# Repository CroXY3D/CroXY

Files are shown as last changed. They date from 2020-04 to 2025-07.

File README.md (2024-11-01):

# CroXY
CroXY is a Crossed Gantry 3D Printer.  Pronounced "Crock-see".  

Designed and built by Wes Cherry (Ocho Camino, wesc@technosis.com) with help from CLedbetter.

CroXY is a fully enclosed 3D CrossXY printer with a crossed linear rail gantry design, direct drive extruder and a kinematically mounted bed that moves in Z with reduced triple belt drive. 

Version 3 is nearing Beta.   

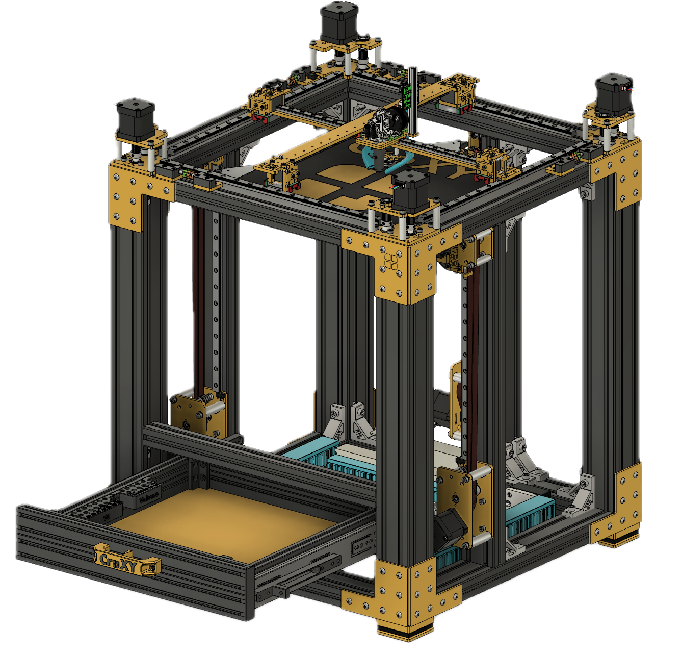
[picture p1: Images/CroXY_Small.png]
Small Image of CroXY
 
  
It is simple to build, align and provision.  The design requires no printed parts aside from the cooling duct.   Print quality is superb. 

The printer has been assembled and is printing with excellent print quality for a many years now.  It is in active development. 

# Major features of CroXY
  - All metal design (Except for cooling duct).  CroXY uses the Ice Cream Sandwich design pattern where printer structures are made from laser cut aluminum plate with standoffs.
  - 3060 frame members for stiffness and ease of assembly.  Corner towers can be 6060.
  - Crossed rail gantry design with 4 motors (5mm or 8mm shafts) driving 9mm or 12mm XY belts.  Motor shafts are supported with a bearing on their end to reduce flex.
  - Triple 4:1 9mm belt driven Z for automatic bed levelling.
  - Linear Rails except the cross rails are MGN12H. 
  - Cross rails are MGN9H for less moving mass.  Both cross rails are backed by a flat 4.7mm thick 6061 aluminum backer.  Extensive FEA simulations have been performed on the gantry.
  - Fully Enclosed, Coming soon!   
  - Bed is 6 to 12mm cast aluminum and is kinematically mounted with Maxwell kinematic joints preloaded by magnets. 
  - Extruders supported: LGX Lite, VZ Hextrudort and Orbiter.
  - Hotends supported: Goliath water and air cooled, Chube.
  - Part cooling is CPAP or dual Axial 4028 fans
  - Magnetically coupled switch based probe (Euclid) picked up from a dock for super accurate bed probing.  Repeatibility of nearly 0.001mm.
  - Simple, easily accessible belt tensioning.
  - Dedicated area for nozzle purge and wipe. 
  - Z Towers are built on a single 3060 extrusion.  They easily remove from the printer for bench work.
  - BTT Octopus, Fysetc Spyder with Klipper, Duet2 or Duet3 electronics with Reprap firmware 3.
  - Electronics are in the bottom of the machine, for easy access from above.  No flipping or rotating the machine to access the electronics.
  - Nearly all wires are run thru the center channel of 3060/6060 extrusions for a clean looking machine.
  - Built in optional drawer for tools and or a spool that feeds the extruder.  
  - Hour meter.
  - LED status rings, similar to BLV MGN Cube.
  - Feet with sorbothane vibration isolation.
  - Footprint comparable to other printers of same bed size (Footprint is only 5% larger than that of a comparable print volume Railcore)
  - CAD is for 300x300x300 nominal size.  CroXYs as small as 200^3 and as large as 500x350x350 have been built. 

# CroXY offers a number of advantages over CoreXY designs
  - Belts are shorter and have simple paths, alignment is easier and less ringing
  - Belts can be as wide as 12mm for more accurate positioning and less ringing compared to 6mm wide belts.
  - Less friction in motion system makes for more accurate positioning making for exceptional layer stacking.
  - 4 motors moving the XY gantry make for more torque for more accurate positioning (1.4x-4x more torque)
  - Motion is simple X motors move X, Y motors move Y, so troubleshooting is easier
  
# Disadvantages of CroXY
  - Requires 3 more rails and 2 more steppers/drivers than a CoreXY.
  - Visibility of the build area is lessened.  Though the printhead has been designed with nozzle visibility in mind.
  - Toolchanging is more difficult, but it is possible.
  - Cost.  It's not a cheap build.
  
# Work to be done 
  - Finish lid and enclosure, including front hinges
  - Wiring diagram
  - Chamber heater
  
# CAVEATS
CroXY is an advanced build.  You should only attempt to build it if you have successfully built another kit printer.  Building that will give you a lot of experience so you don't make mistakes with CroXY.  

Croxy is a ever growing experimental project. Although the existing machines work and work well, there is no guarantee that yours will. These are homemade machines built by different people, with differing parts. We help where we can, but in the end this is a hobby and we are hobbiests.

# DISCORD
We now have a [Discord](https://discord.gg/ryj6wyx) to discuss CroXY!  

# BOM  
A CroXY build will cost approx $XXXX with budget rails.  A first class build with Misumi rails will run around $XXXX. 

# SOURCE FILES
CroXY is fully open source with .STP files provided.  Please check the license (Creative Commons Attribution-NonCommercial-ShareAlike 4.0 International) before modifying or deriving from CroXY.  Commercial use or sale of CroXY derived designs is prohibited without approval.

# MEDIA

The images are quite old.  Will update soon.

[Video of CroXY](https://youtu.be/Kx4VfzS_V6c)

[Video of CroXY bed probiing and automatic bed levelling](https://www.youtube.com/watch?v=WyJbbjh8Hpk)

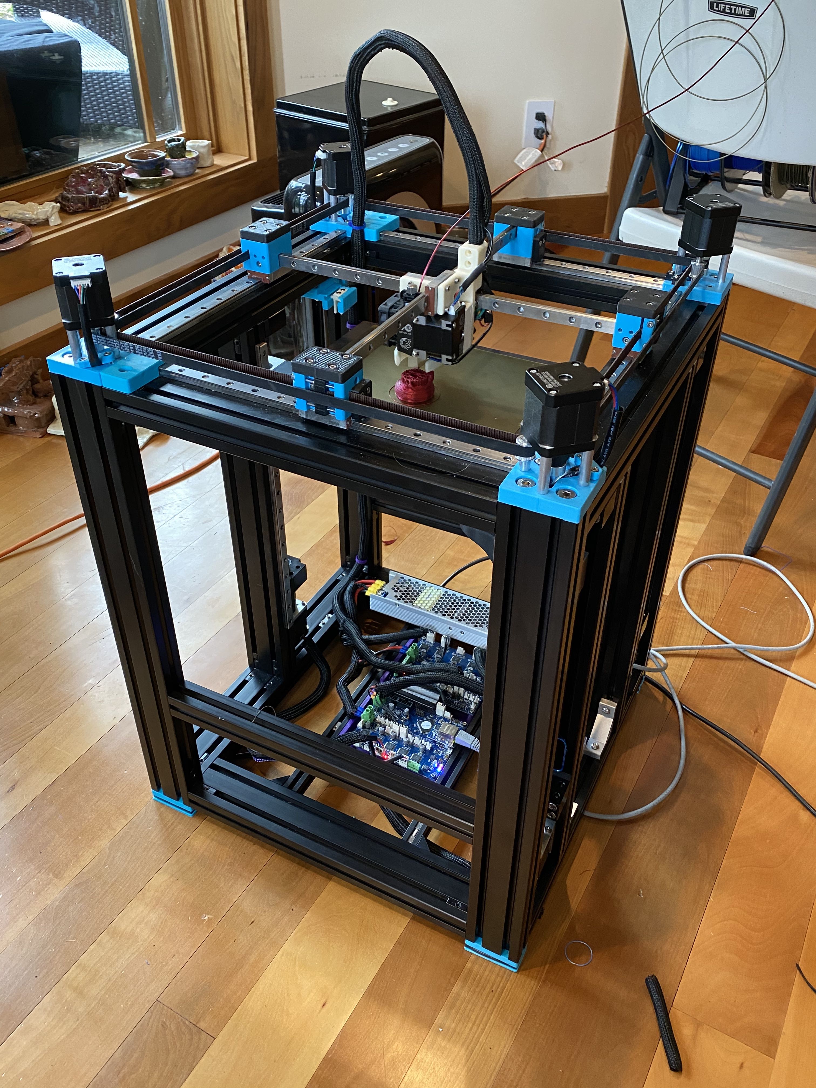
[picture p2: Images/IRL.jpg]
IRL


Older picture of CroXY.  It currently looks like the renderings IRL.

Image of CroXY
  
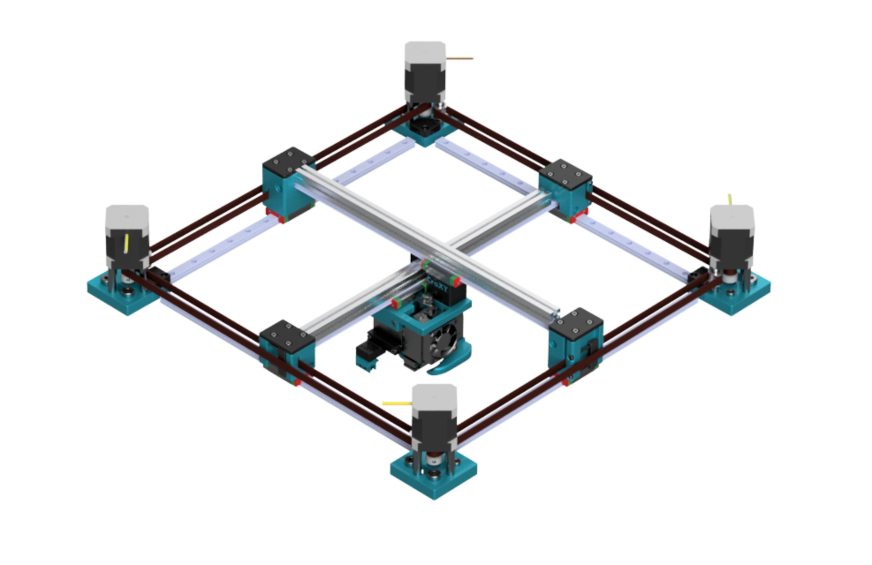
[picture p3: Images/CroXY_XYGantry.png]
Image of CroXY XY Gantry


XY Gantry

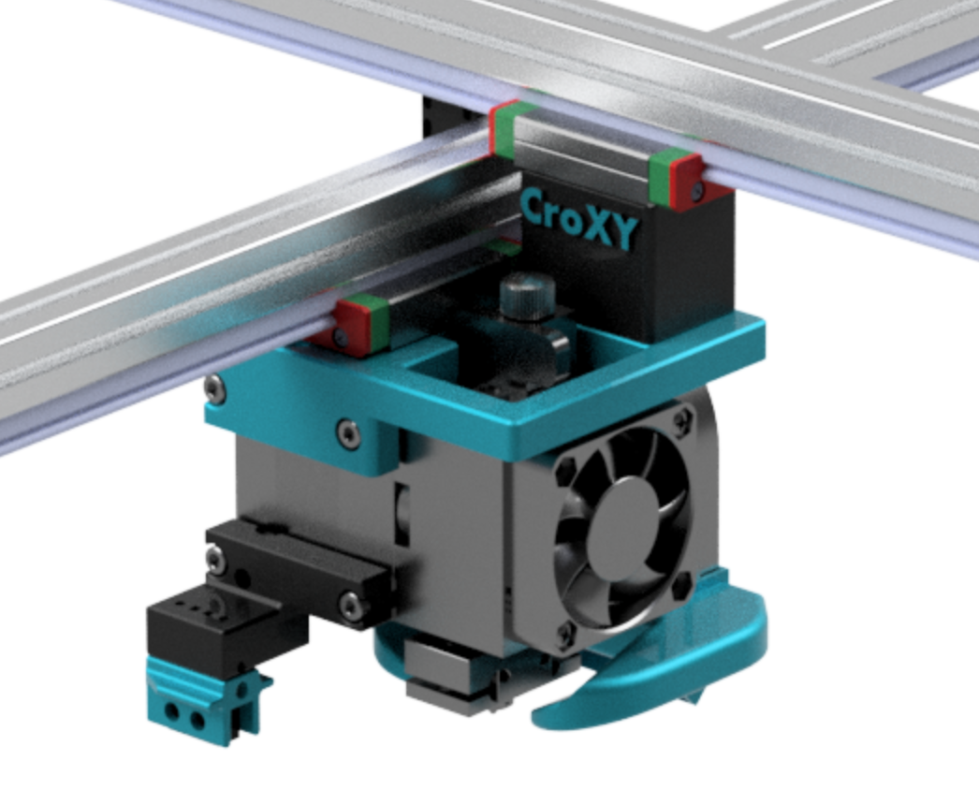
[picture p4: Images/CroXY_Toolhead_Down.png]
Image of CroXY Toolhead Down


Toolhead

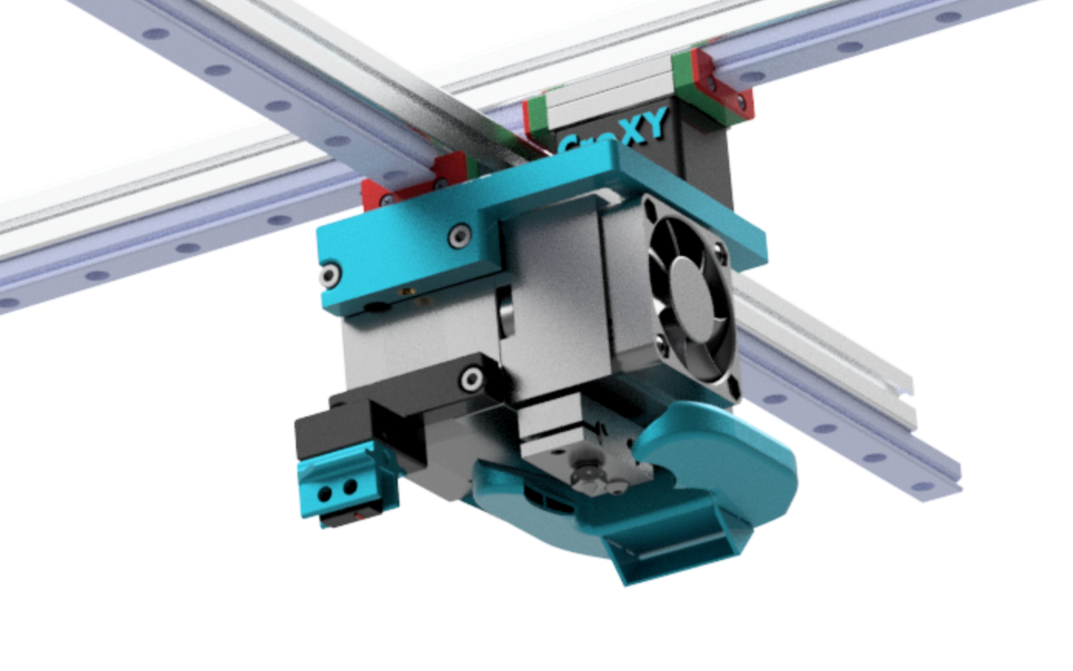
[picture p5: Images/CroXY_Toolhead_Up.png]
Image of CroXY Toolhead Up


Toolhead

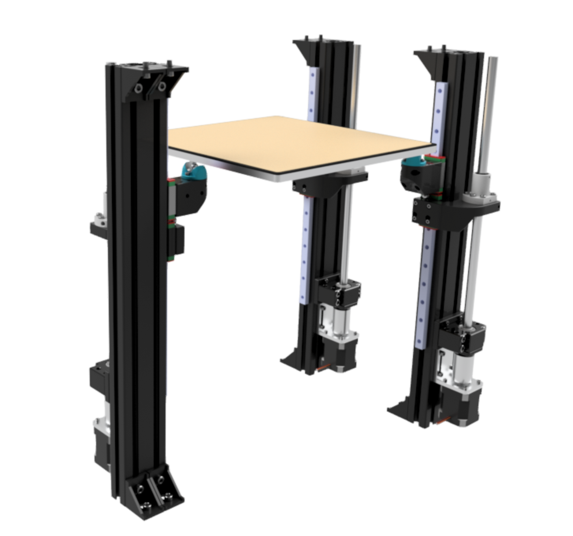
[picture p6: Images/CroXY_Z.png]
Image of CroXY Z


Z and Bed

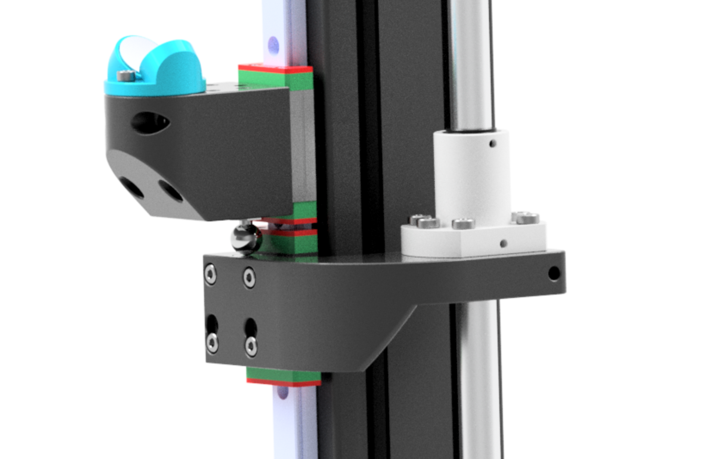
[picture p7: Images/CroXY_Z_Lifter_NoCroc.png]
Image of CroXY Z Lifter NoCroc


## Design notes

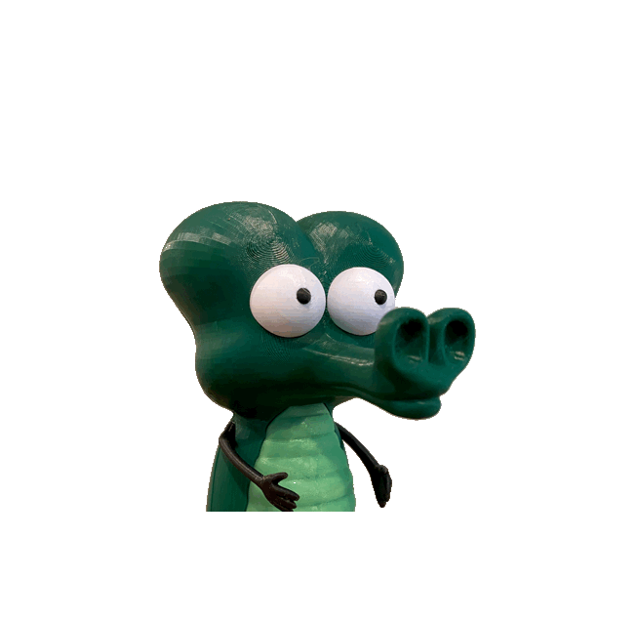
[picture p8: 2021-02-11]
Images/Discord/CroxyTransparentWideMargins.png

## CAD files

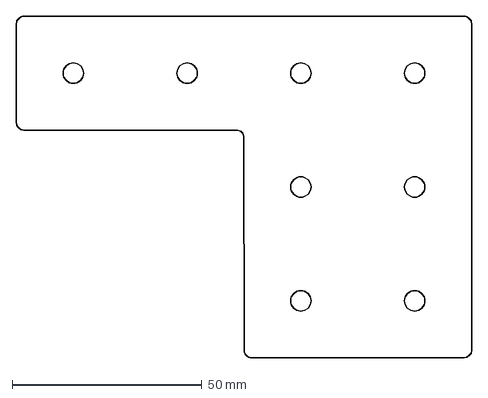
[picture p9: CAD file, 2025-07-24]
DXF/Frame/Corner_Bracket_3_3060CornerPost_x7_6060CornerPost_x15.DXF
120.0 x 90.0 mm

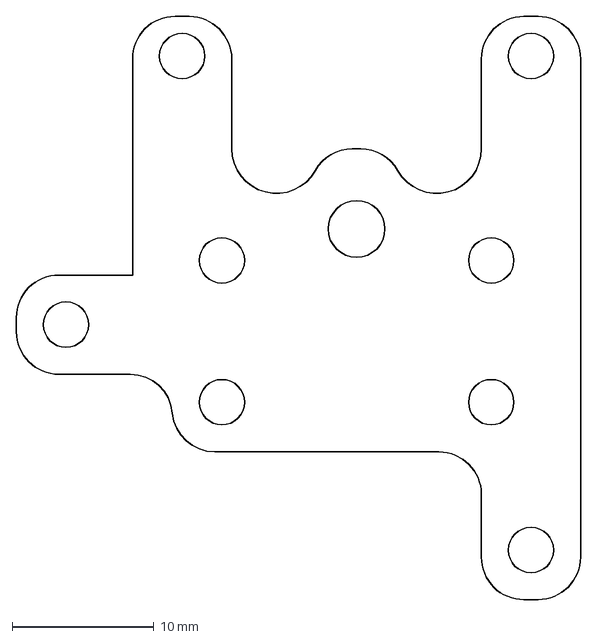
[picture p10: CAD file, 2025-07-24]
DXF/HeLGX_Adapter_3_X1.DXF
39.8 x 41.2 mm

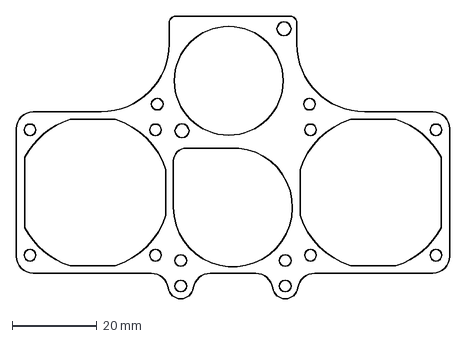
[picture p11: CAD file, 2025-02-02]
DXF/Tool/T_PCF_Axial_Fan_Adapter_3_x1.DXF
102.0 x 66.5 mm

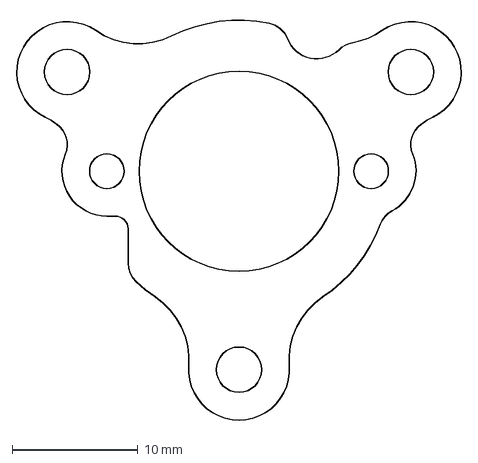
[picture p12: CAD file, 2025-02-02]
DXF/XY/XY_Motor_Bearing_Housing_5_x4.DXF
35.4 x 32.3 mm

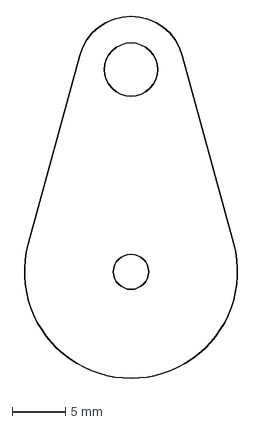
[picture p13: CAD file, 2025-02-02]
DXF/Z/Z_Maxwell_Spring_1_SpringSteel_x3.DXF
21.5 x 34.6 mm

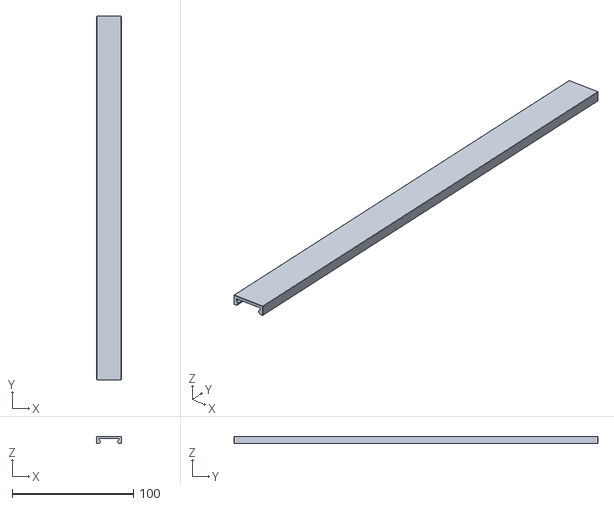
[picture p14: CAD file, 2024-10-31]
STL/Electronics/A-Cable_Duct_2020_300mm_Cap-T.stl
20.3 x 300.0 x 6.00

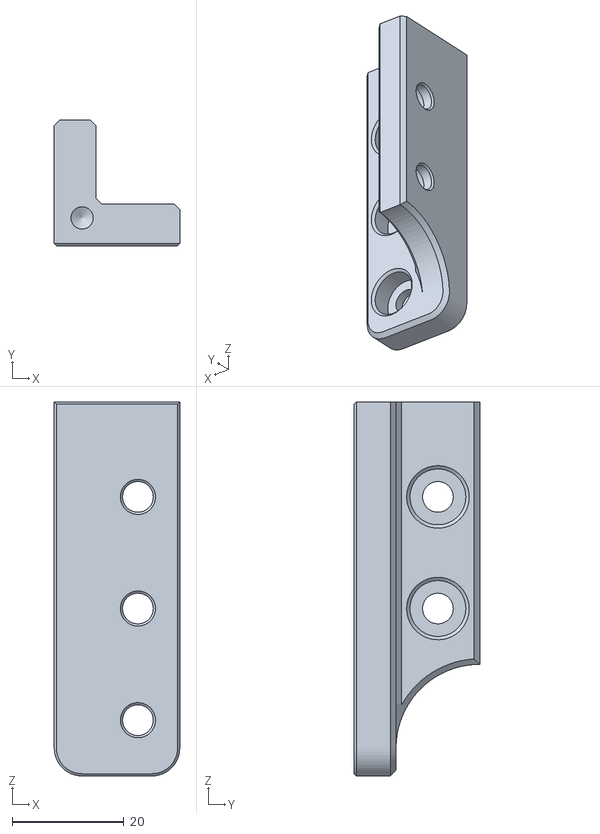
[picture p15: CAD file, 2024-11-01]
STL/Frame/B-Drawer_Corner_Front_Right-F.stl
22.5 x 22.5 x 67.0

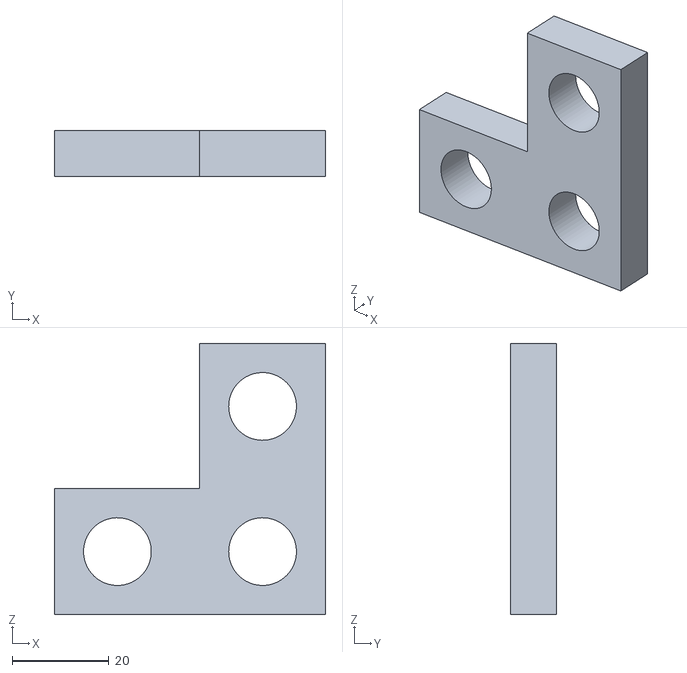
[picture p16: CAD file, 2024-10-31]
STL/Helpers/B-Sorbothane_Template-F.stl
56.0 x 9.52 x 56.0

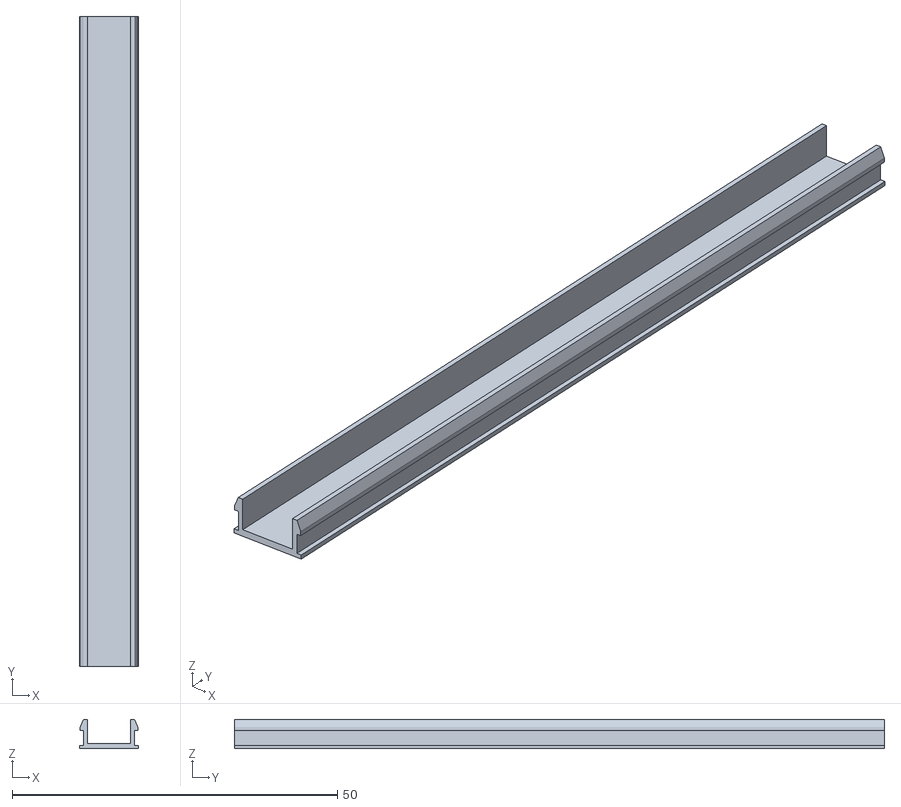
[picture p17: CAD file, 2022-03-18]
STL/Misc/A-Slot_Covers_LED_Scale_Appropriately.stl
9.00 x 100.0 x 4.51

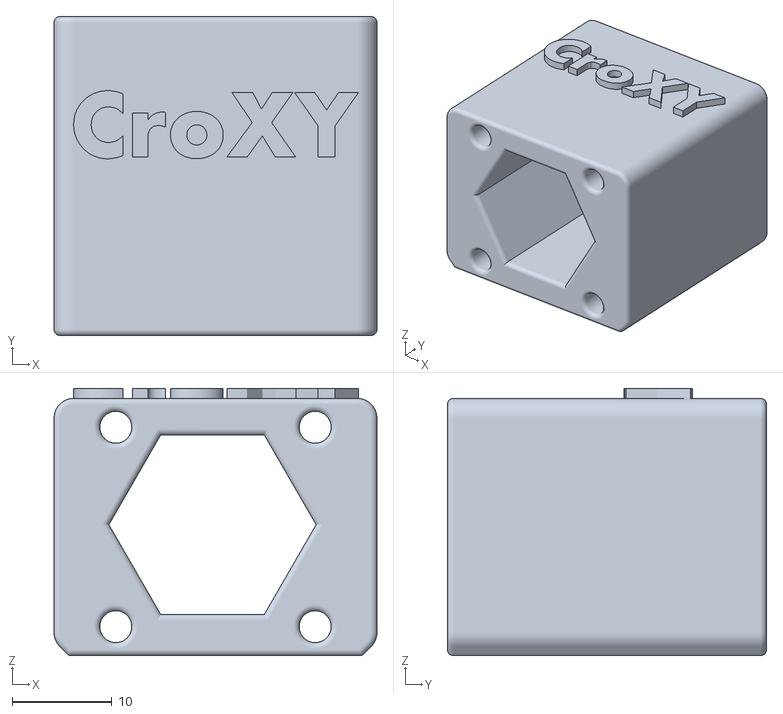
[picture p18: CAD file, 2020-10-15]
STL/Tool_Hemera/B-Hemera_Spacer_32.stl
32.4 x 32.0 x 26.8

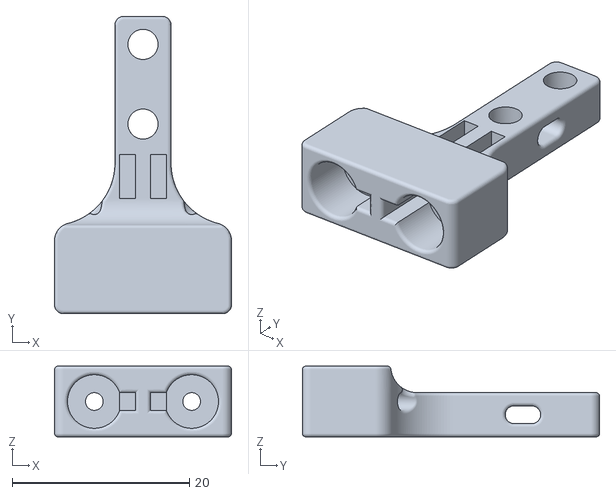
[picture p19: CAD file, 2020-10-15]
STL/Tool_Hemera_Crux/B-Probe-Pickup.stl
20.0 x 33.6 x 8.00

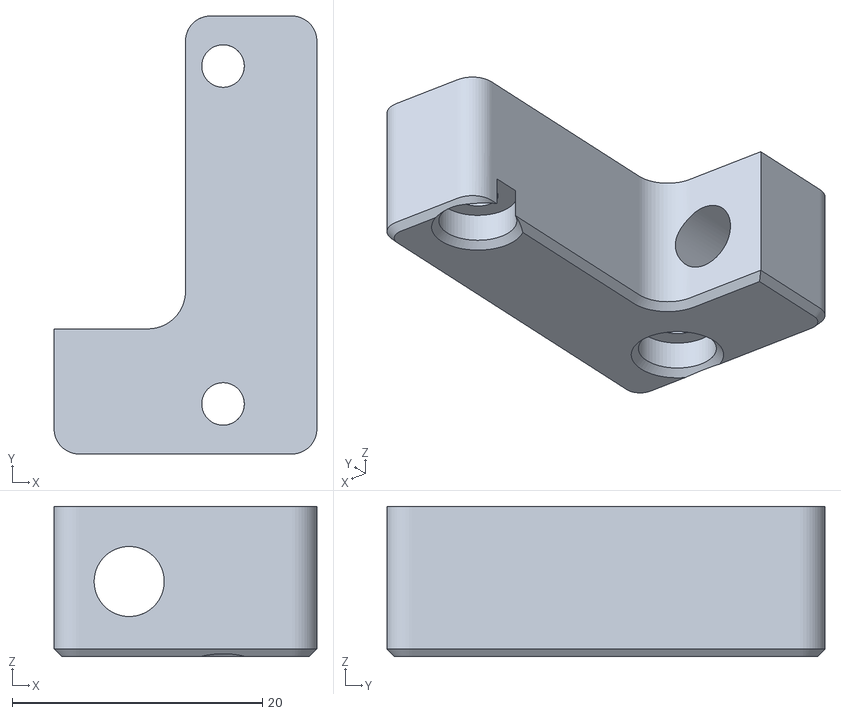
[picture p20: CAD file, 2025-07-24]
STL/XY/A-Tensioner Moving_Block_M4_x4-X.stl
21.0 x 35.0 x 12.0

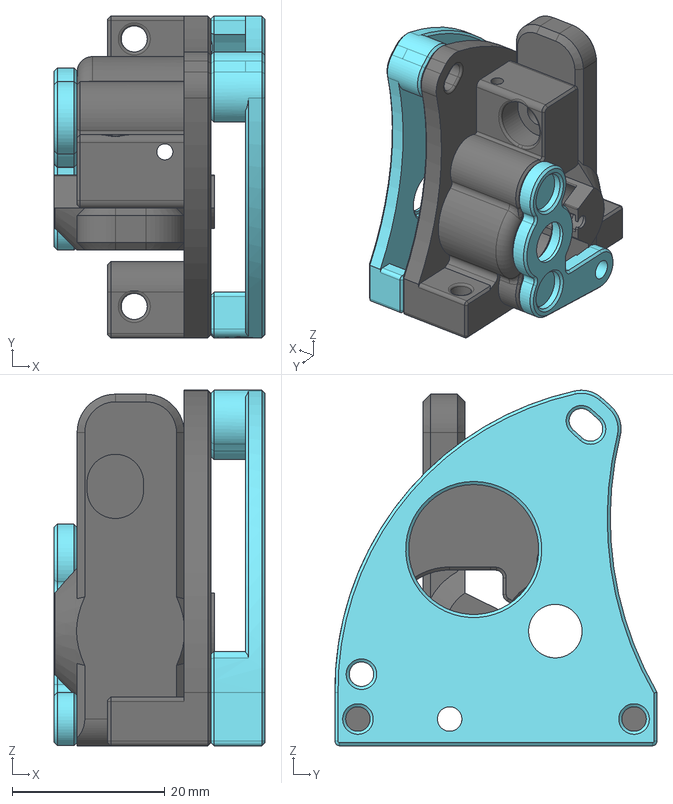
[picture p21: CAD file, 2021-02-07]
STP/Sailfin/Sailfin v70.step
27.6 x 42.1 x 46.5 mm
Rear
Mid
Lever
Front

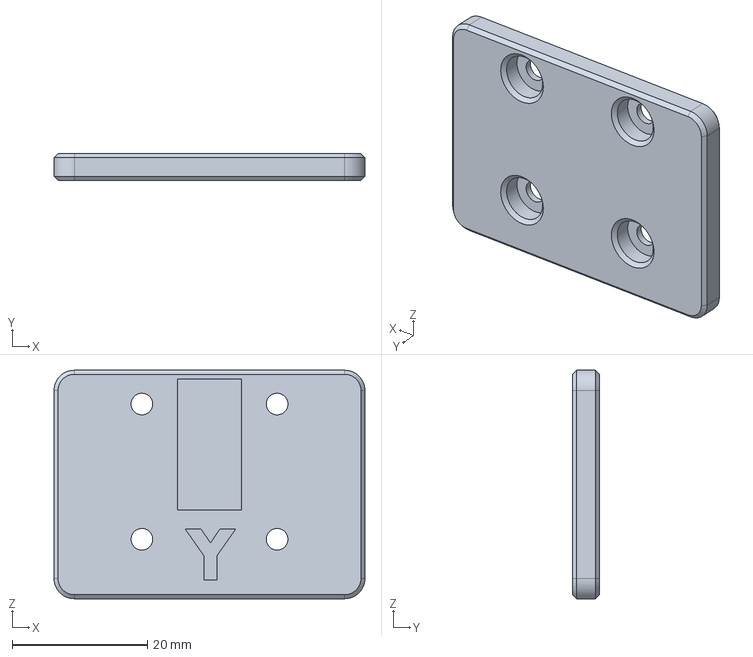
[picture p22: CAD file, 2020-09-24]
STP/XY/B-Y_Carriage_Cap_1215_2-B.stp
46.0 x 4.00 x 33.8 mm

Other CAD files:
STP/MicroXY_Spacer_3_X1.stp
DXF/Frame/Corner_Bracket_3_3060CornerPost_x8.DXF
DXF/Plate_Spacer_3_X1.DXF
DXF/Tool/T_Hotend_Goliath_WC_Short_Adapter_3_x1.DXF
DXF/Frame/Corner_Bracket_3_3030_x7_6060_x15.DXF
DXF/Frame/Corner_Bracket_3_3030_x8.DXF
DXF/Frame/Corner_Bracket_CroXY_Logo_3_x1.DXF
DXF/Lower_Plate_3_X1.DXF
DXF/MicroXY_HeLGX_Adapter_3_X1.DXF
DXF/MicroXY_Lower_Plate_3_X1.DXF
DXF/MicroXY_Plate_Spacer_3_X1.DXF
DXF/MicroXY_Standoff_Beacon_2_5_5052_X1.DXF
DXF/MicroXY_Teakettle_Extruder_Adapter_3_x1.DXF
DXF/MicroXY_Teakettle_Plate_5_x1.DXF
DXF/MicroXY_Turkey_Bacon_1Ti5_X1.DXF
DXF/Microxy_Plate_3_X1.DXF
DXF/Tool/PCF_Front_CPAP_Adapter_3_x1.DXF
DXF/Tool/T_Bottom_Mount_3_x1.DXF
DXF/Tool/T_Extruder_LGXlite_VZ_ChubeConduction_3_x1.DXF
DXF/Tool/T_Extruder_LGXlite_VZ_Goliath_Dragon_ChubeAir_3_x1.DXF
DXF/Tool/T_Hotend_Chube_Adapter_3_x1.DXF
DXF/Tool/T_Hotend_GoliathAir_Dragon_Adapter_3_x1.DXF
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

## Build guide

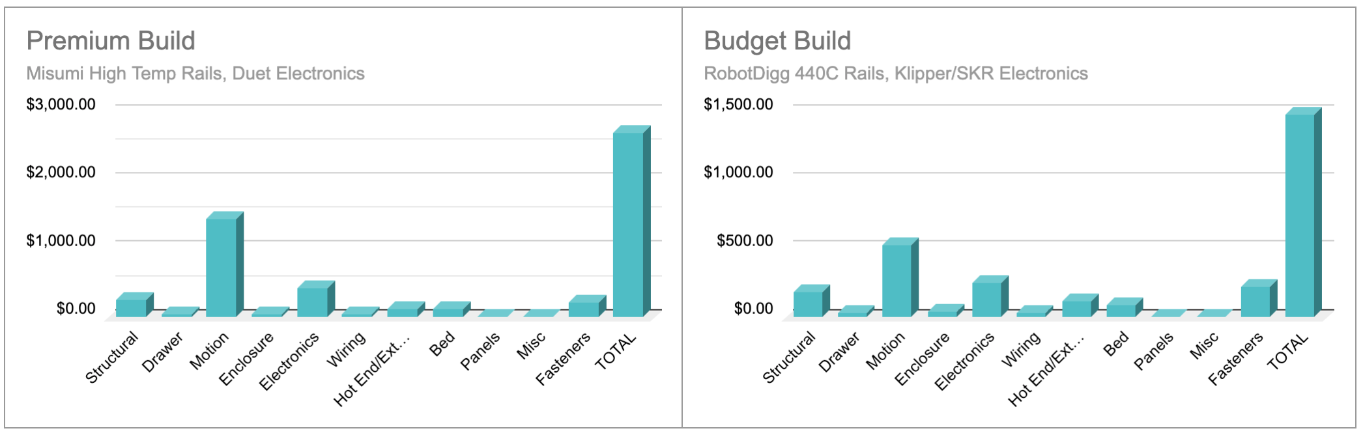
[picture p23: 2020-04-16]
Images/Build_Cost.png

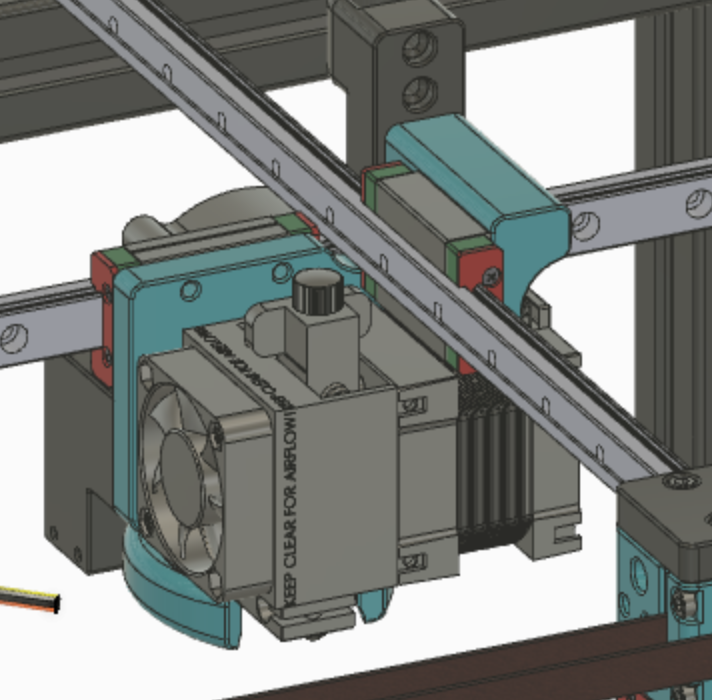
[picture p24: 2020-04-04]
Images2/Printhead.png

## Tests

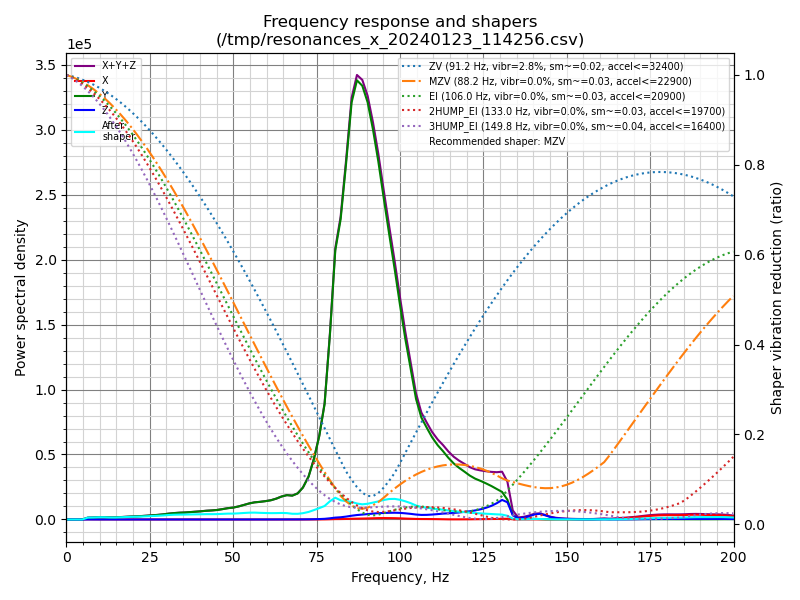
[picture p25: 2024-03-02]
IS/2nd/shaper_calibrate_x.png

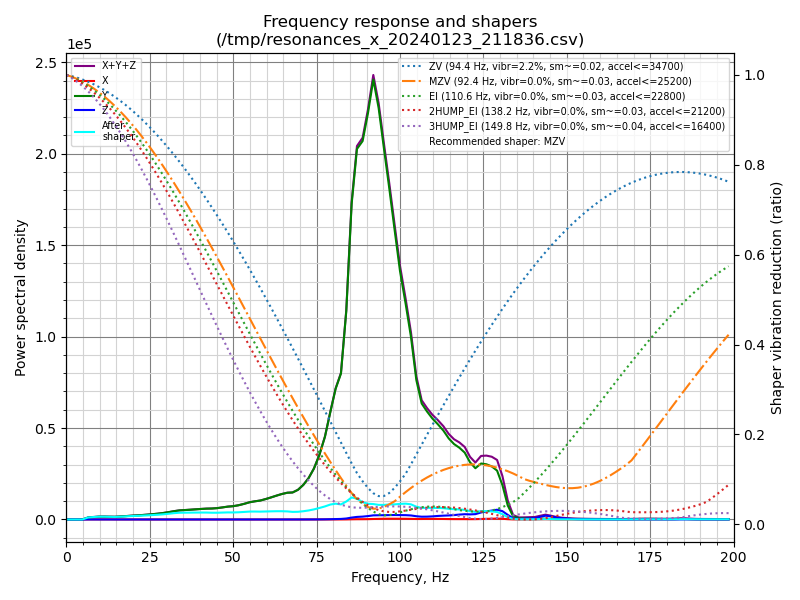
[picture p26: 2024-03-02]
IS/4th x rail every screw/shaper_calibrate_x.png

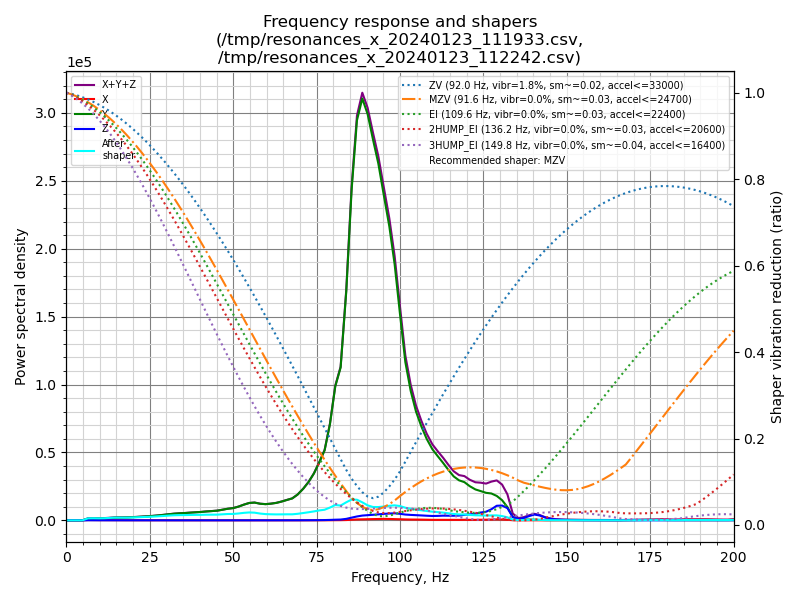
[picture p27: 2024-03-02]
IS/Initial/shaper_calibrate_x.png

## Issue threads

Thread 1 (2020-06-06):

Question: Fusion model?

imbaimbaimba, 2020-06-06:
Hey there! Cool project you got going on. I was interested to look a little through the Fusion model that you mention should be there, albeit maybe not totally up to date. I could not find the Fusion model anywhere though. Can you link it to me?

basic-tv, 2020-07-09:
Could you also share the fusion model with me?

wesc23, 2020-07-09:
Hi, sorry, @imbaimbaimba, i just got this message.  Here's a public link to the F360 file.   I had to recreate it due to Fusion being Fusion, and haven't integrated the enclosure and electronics back into the model yet.  The orange cap on the toolhead is work in progress and may not be in final release (has interferences with the rails).

https://a360.co/3gxpcK5

wesc23, 2020-07-09:
The files in the .git are also currently quite out of date.  I am putting together things so i can update in next couple days.

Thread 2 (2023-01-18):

A problem was found with the length of the Y Frame of the BOM table

xiaopi321, 2023-01-18:
Hello, creator of CroXY. I want to assemble a 300 * 300 * 300 CroXY, but I found that I changed the printing stroke in the CroXY BOM to 300 * 300 * 300. Isn't the HFSB6-3060 length of Y Frame and X Frame both 420 mm? The BOM shows that the Y frame needs 480mm, which makes the Y Cross Rail 2020 Stiffener unable to assemble the HFSC5-2020 of the Y Cross Rail 2020 Stiffener. Do I need to cut the Y frame out of 60mm?
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
@CroXY3D

CroXY3D, 2023-01-18:
Hi,  Great to hear you are building one!For the 6060 corner version.  The x and y frame members should be the same length.    The BOM automatically do this if you select the 6060 corner version.    (On the calcumilator sheet.   Looks like I need to fix the bom page to better support 6060.)Come join us on discord for more help with the build!Join the CroXY Discord Server!discord.ggSend a message to #croxy-build and I’ll set your server permissions -'//esOn Jan 18, 2023, at 4:24 AM, xiaopi321 ***@***.***> wrote:
Hello, creator of CroXY. I want to assemble a 300 * 300 * 300 CroXY, but I found that I changed the printing stroke in the CroXY BOM to 300 * 300 * 300. Isn't the HFSB6-3060 length of Y Frame and X Frame both 420 mm? The BOM shows that the Y frame needs 480mm, which makes the Y Cross Rail 2020 Stiffener unable to assemble the HFSC5-2020 of the Y Cross Rail 2020 Stiffener. Do I need to cut the Y frame out of 60mm?

@CroXY3D

—Reply to this email directly, view it on GitHub, or unsubscribe.You are receiving this because you were mentioned.Message ID: ***@***.***>

xiaopi321, 2023-03-06:
> 嗨，很高兴听到您正在建造一个！对于 6060 角版本。x 和 y 框架成员的长度应相同。如果选择 6060 拐角版本，BOM 会自动执行此操作。（在煅烧器片上。看起来我需要修复 bom 页面以更好地支持 6060。快来加入我们的不和谐，以获得有关构建的更多帮助！加入 CroXY Discord 服务器！discord.gg发送消息到 #croxy-build，我将设置您的服务器权限 -'//es在 18 年 2023 月 4 日凌晨 24：321，xiaopi300 ***@***.***> 写道： 你好，CroXY的创造者。我想组装一个 300 * 300 * 300 CroXY，但我发现我将 CroXY BOM 中的打印笔划更改为 300 * 300 * 6。HFSB3060-420 的 Y 型和 X 型车架的长度不是都是 480 毫米吗？BOM显示Y型车架需要2020mm，这使得Y横轨5加劲肋无法组装Y横轨2020加劲肋的HFSC2020-60。我需要将 Y 型框架从 3mm 中切割出来吗？@CroXY<>D —直接回复此电子邮件、在 GitHub 上查看或取消订阅。您收到此消息是因为您被提及。消息 ID：***@***.***>

Hi, friend, I have another problem. Is the Z belt closed? How to link the Z-axis belt if it is not a closed belt? Can share the latest version of CroXY Parameterized. step

Would you like to share the file? In the future, you need to use the Acrylic plate to seal the printer, and you need to use the complete. step file. thank you

xiaopi321, 2023-03-22:
@CroXY3D Hi, friend, I want to know how the Z-axis timing belt is fixed to the elevator. If I jam the timing belt in the slot, it will automatically fall off
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

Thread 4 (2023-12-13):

Filament Sensor Orbiter

elpilla, 2023-12-13:
First of all thank you for this fabulous extruder, talking to the modder who created the modification I told him that it would be great if you could put the filament sensor of the orbiter in it and he has created the following modification for the mirror version (it is the one used by the KP3S mod) I leave the link in case it is of interest.
https://www.printables.com/model/282299-sailfin-extruderremix
Again, thank you for this fabulous extruder

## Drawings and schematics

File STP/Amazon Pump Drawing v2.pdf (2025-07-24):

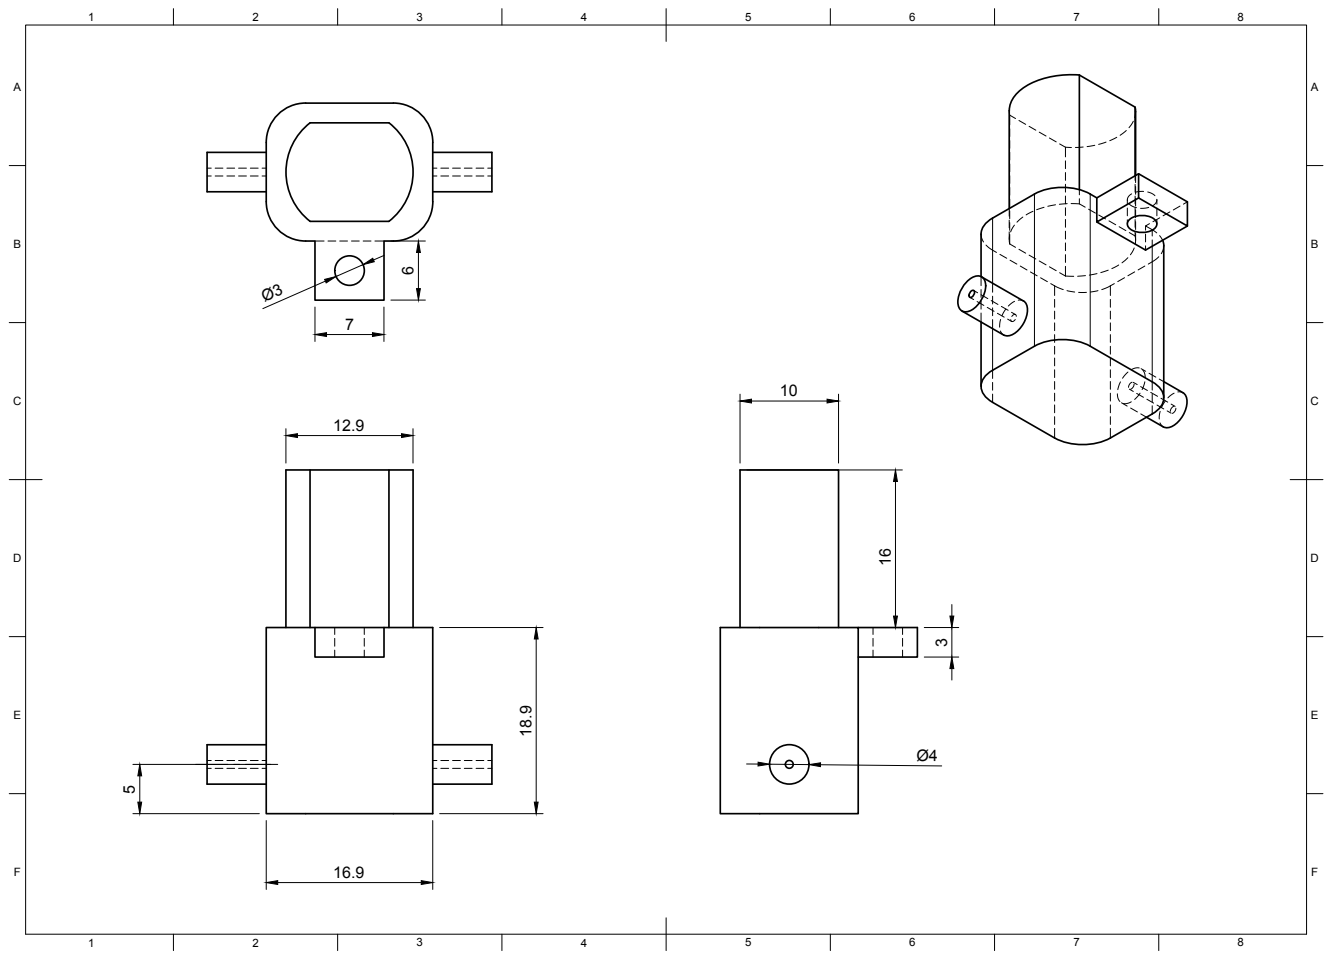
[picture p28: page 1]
8 BCDEF; ABCDEF

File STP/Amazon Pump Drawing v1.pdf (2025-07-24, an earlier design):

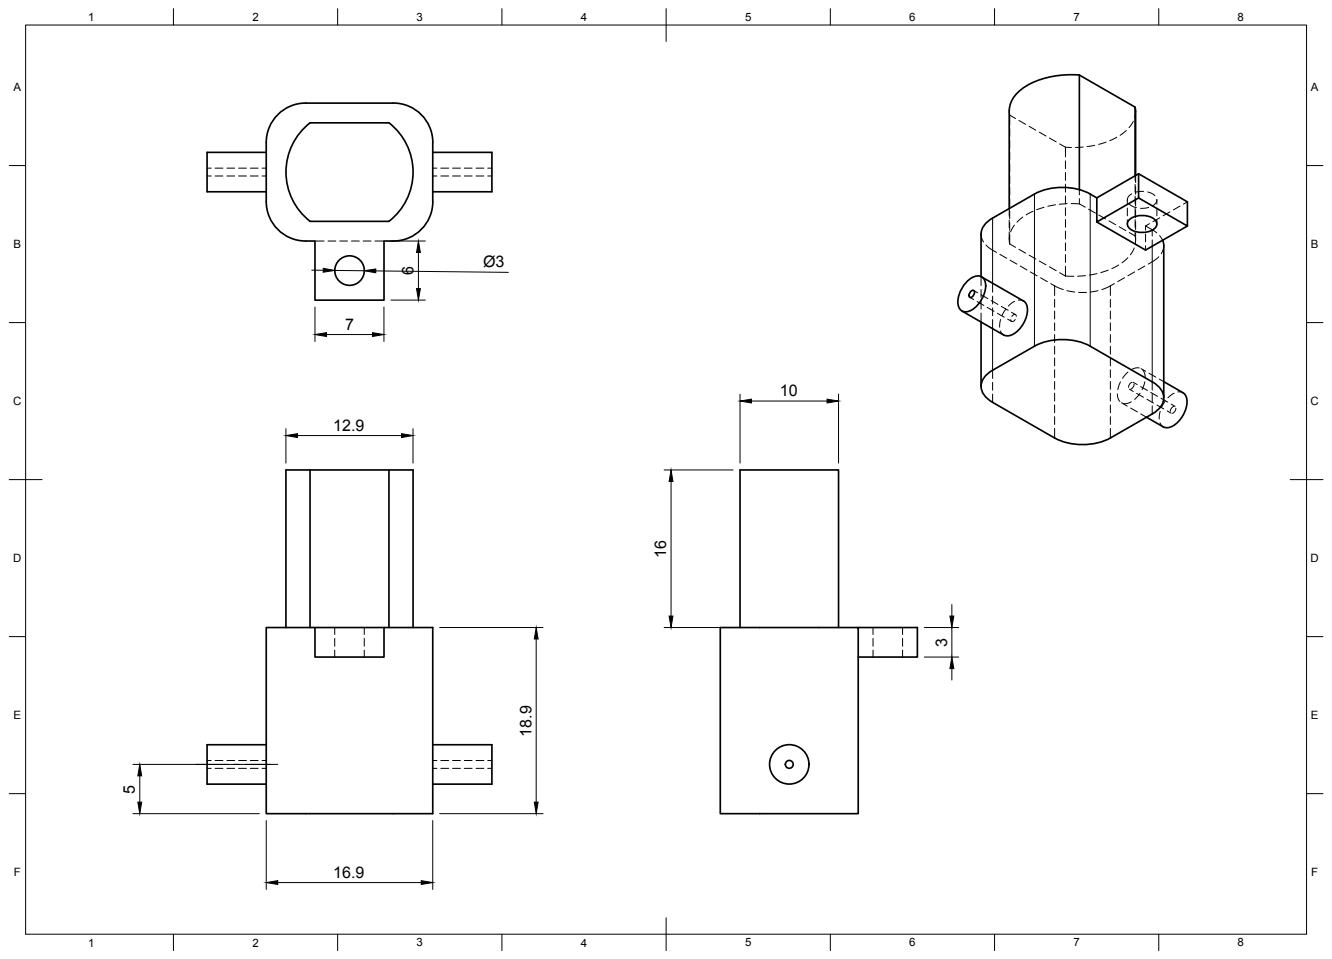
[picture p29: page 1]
8 BCDEF; ABCDEF

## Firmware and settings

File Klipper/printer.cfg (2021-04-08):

##### AUTOCREATED BY KIAUH #####
#[include kiauh.cfg]
############################################################## 
#
# CroXY Klipper printer.cfg
#
# Croxy is a crossed gantry auto bed levelling 3d printer, with XY driven by 4 motors.  Z by three independent motors.
#
# This is for a Fysetc S6 as the controller for X,X1,Y,Y1 and E
# Z is handled by a BigTreeTech SKR 1.3 (was another S6, but reasons)
#
# FYSETC S6
#   STEP_XFL : Front Left X Stepper connected to X Stepper
#   STEP_XBR : Back Right X Stepper connected to Z Stepper
#   STEP_YFR : Front Right Y STepper connected to E2 Stepper
#   STEP_YBL : Back Left Y Stepper connected to E1 Stepper 
#   STEP_EXT : Extruder connected to E0 Stepper 
#
#   Z Stepper socket on my board has failed
#
#    YBLo------------XBR
#     |               o
#     |               |
#     |               | 
#     |               |
#     o               |
#     XFL-----------oYFR
#
#     Steppers, o = idler
#
#   ES_XFR  : Endstop X Front Right (at Xmax), connected to X- 
#   ES_XBR  : Endstop X Back Right (at Xmax), connected to X+
#   ES_YFL  : Endstop Y Front Left (at Y Min), connected to Y-
#   ES_YFR  : Endstop Y Front Right (at Y Min), connected to Y+
#
#     +------------XBR+
#     |               |
#     |               |
#     |               | 
#     |               |
#     YFL            YFR  
#     +------------XFR+
#
#     Endstop Positions
#
#
#
#
#   TBD, Heaters, Thermistors
#
# SKR 1.3, 2nd MCU
#   STEP_ZL  : Left Z Stepper connected to X Stepper
#   STEP_ZR  : Right Z Stepper connected to Z Stepper
#   STEP_ZB  : Back Z Stepper connected to Y Stepper
#
#     +-------ZB------+
#     |               |
#     |               |
#     |               | 
#     ZL              ZR
#     |               |  
#     +---------------+
#
#     Z Stepper Positions
##############################################################


 
 

#define Fysetc S6 as primary MCU
[mcu]
serial: /dev/serial/by-id/usb-Klipper_stm32f446xx_27002E000851363131343032-if00
restart_method: command


[board_pins]
aliases:
    STEPX=PE11, DIRX=PE10, ENX=!PE12


[printer]
kinematics: cartesian
max_velocity: 500
#max_accel: 7000
max_accel: 20000  # Klipper resonance
max_accel_to_decel: 20000 # Klipper resonance
square_corner_velocity: 5.0
max_z_velocity: 200
max_z_accel: 1000

#Gcode G2/G3 Arc Support
[gcode_arcs]
resolution: 0.1


# Input Shaper Settings (CroXY 500x350 with 1515 backers below and Hemera Toolhead
[input_shaper]
shaper_freq_x: 64.6
shaper_type_x: zv
shaper_freq_y: 46.4
shaper_type_y: zv


[idle_timeout]
gcode:
  TURN_OFF_HEATERS
timeout: 1800


# Fans  
# Hotend Cooling Fan
[heater_fan extruder_fan]
# connected to Fan0 on S6 #1 - 12v Fan
pin: PB0
max_power: 1.0
hardware_pwm: false
kick_start_time: 0.500
heater: extruder
heater_temp: 50.0
fan_speed: 1.00
 
# print cooling fan
[fan]
# connected to Fan1 on S6 #1 - 24v Fan.  24V comes from HE+ via Toolboard
pin: PB1
max_power: 1.0
kick_start_time: 0.100
  
#fan for printed model FAN0
#[fan]
#pin: PB0 


#	S6 and skr cooling fan
[heater_fan electronics]
# connected to Fan2 on S6 - 12v Sunon Blowers in parallel, one for SKR, one for S6
pin: PB2
max_power: 1.0
kick_start_time: 0.500
heater: extruder
heater_temp: 20.0
fan_speed: 0.3


# Steppers

# STEP_XFL : Front Left X Stepper connected to X Stepper, homes to Xmax, connected X-
[stepper_x]
step_pin: PE11
dir_pin: !PE10
enable_pin: !PE12
# 0.9deg - 20T pulley -> (400 steps/rev*16 usteps/step)/(20 teeth*2 mm/teeth) = 160 steps per mm - 1/16 microstepping
step_distance: 0.00625
# not connected to virtual endstop
#endstop_pin: tmc2209_stepper_x:virtual_endstop 
endstop_pin: ^PB14  # PA1 for X-max  PB14 for X-min
position_min: -260
position_endstop: 250
position_max: 250
homing_speed: 65.0
homing_retract_dist: 2.0
second_homing_speed: 10
#homing_positive_dir: True


# STEP_XBR : Back Right X Stepper connected to E1 Stepper, homes to Xmax, connected to X+
[stepper_x1]
step_pin: PE6 #E1
dir_pin: PC13 #E1
enable_pin: !PE5 #E1
# 0.9deg - 20T pulley -> (400 steps/rev*16 usteps/step)/(20 teeth*2 mm/teeth) = 160 steps per mm - 1/16 microstepping
step_distance: 0.00625
# not connected to virtual endstop
#endstop_pin: tmc2209_stepper_x1:virtual_endstop 
endstop_pin: ^PA1   # PA1 for X-max  PB14 for X-min 

 

#STEP_YFR : Front Right Y Stepper connected to Y Stepper, homes to Ymin, connected Y+ pin
[stepper_y]
step_pin: PD8
dir_pin: !PB12
enable_pin: !PD9
# 0.9deg - 20T pulley -> (400 steps/rev*16 usteps/step)/(20 teeth*2 mm/teeth) = 160 steps per mm - 1/16 microstepping
step_distance: 0.00625
# not connected to virtual endstop
# endstop_pin: tmc2209_stepper_y:virtual_endstop 
endstop_pin: ^PA2  # PA2 for Y-max, PB13 for Y-min
position_min: -185
position_endstop: -185
position_max: 165
homing_speed: 65.0
homing_retract_dist: 2.0
second_homing_speed: 10
#homing_positive_dir: False

# STEP_YBL : Back Left Y Stepper connected to E2 Stepper, homes to Ymin, connected Y- pin
[stepper_y1]
step_pin: PE2 #E2
dir_pin: PE4 #E2
enable_pin: !PE3 #E2
# 0.9deg - 20T pulley -> (400 steps/rev*16 usteps/step)/(20 teeth*2 mm/teeth) = 160 steps per mm - 1/16 microstepping
step_distance: 0.00625
# not connected to virtual endstop
#endstop_pin: tmc2209_stepper_y1:virtual_endstop 
endstop_pin: ^PB13  # PA2 for Y-max PB13 for Y-min

# STEP_EXT
[extruder]
# connected to E0 Stepper on S6 #1
step_pin: PD5
dir_pin: !PD6
enable_pin: !PD4
step_distance: 0.00244498777506
nozzle_diameter: 0.400
filament_diameter: 1.750
max_extrude_only_distance: 1400.0
max_extrude_only_velocity: 120.0
max_extrude_only_accel: 15000.0
max_extrude_cross_section: 20000.0



heater_pin: PB3 # E0 OUT
sensor_type: EPCOS 100K B57560G104F
sensor_pin: PC0  # TE0
control: pid
pid_Kp: 22
pid_Ki: 1.08
pid_Kd: 114
min_temp: 0
max_temp: 270
smooth_time: 3.0
max_power: 1.0
#pressure_advance: 0.05
#pressure_advance_smooth_time: 0.040




#TMC Stepper Driver Settings
[tmc2209 stepper_x]
# connected to X Stepper on S6 
uart_pin: PE8
tx_pin: PE9
microsteps: 16
stealthchop_threshold: 0

#stealthchop_threshold: 9999
interpolate: True
run_current: 1.2  # 42STH60-2004MAC	2A
hold_current: 0.8
sense_resistor: 0.110
# Place a jumper on the two pin header near the endstop for sensorless homing
#diag_pin: PB14 #connected to X- Endstop (X Jumper Header)
#driver_SGTHRS: 115
# TMC driver custom tuning for LDO Motor
driver_IHOLDDELAY: 8
driver_TPOWERDOWN: 20
driver_TBL: 2
driver_TOFF: 3
driver_HEND: 5
driver_HSTRT: 3
driver_PWM_AUTOGRAD: True
driver_PWM_AUTOSCALE: True
driver_PWM_LIM: 12
driver_PWM_REG: 8
driver_PWM_FREQ: 1
driver_PWM_GRAD: 14
driver_PWM_OFS: 36

[tmc2209 stepper_x1]
# was connected to E1 Stepper on S6 but Z socket is defective
uart_pin: PC5 # E1
tx_pin: PC4 #E1
microsteps: 16
stealthchop_threshold: 0

#stealthchop_threshold: 9999
interpolate: True
run_current: 1.2  # 42STH60-2004MAC	2A
hold_current: 0.8
sense_resistor: 0.110
# Place a jumper on the two pin header near the endstop for sensorless homing
#diag_pin: PB13 #connected to Y- Endstop (Y Jumper Header)
#driver_SGTHRS: 115
# TMC driver custom tuning for LDO Motor
driver_IHOLDDELAY: 8
driver_TPOWERDOWN: 20
driver_TBL: 2
driver_TOFF: 3
driver_HEND: 5
driver_HSTRT: 3
driver_PWM_AUTOGRAD: True
driver_PWM_AUTOSCALE: True
driver_PWM_LIM: 12
driver_PWM_REG: 8
driver_PWM_FREQ: 1
driver_PWM_GRAD: 14
driver_PWM_OFS: 36

[tmc2209 stepper_y]
# connneted to Y Stepper on S6 
uart_pin: PE13
tx_pin: PE14
microsteps: 16
stealthchop_threshold: 0

#stealthchop_threshold: 9999
interpolate: True
run_current: 1.2  # 42STH60-2004MAC	2A
hold_current: 0.8
sense_resistor: 0.110
# Place a jumper on the two pin header near the endstop for sensorless homing
#diag_pin: PA3 #connected to Z+ Endstop (E0 Jumper Header)
#driver_SGTHRS: 115
# TMC driver custom tuning for LDO Motor
driver_IHOLDDELAY: 8
driver_TPOWERDOWN: 20
driver_TBL: 2
driver_TOFF: 3
driver_HEND: 5
driver_HSTRT: 3
driver_PWM_AUTOGRAD: True
driver_PWM_AUTOSCALE: True
driver_PWM_LIM: 12
driver_PWM_REG: 8
driver_PWM_FREQ: 1
driver_PWM_GRAD: 14
driver_PWM_OFS: 36

[tmc2209 stepper_y1]
# connected to E2 Stepper on S6 
uart_pin: PE0
tx_pin: PE1
microsteps: 16
stealthchop_threshold: 0

#stealthchop_threshold: 9999
interpolate: True
run_current: 1.2  # 42STH60-2004MAC	2A
hold_current: 0.8
sense_resistor: 0.110
# Place a jumper on the two pin header near the endstop for sensorless homing
#diag_pin: PA2 #connected to Y+ Endstop (E1 Jumper Header)
#driver_SGTHRS: 115
# TMC driver custom tuning for LDO Motor
driver_IHOLDDELAY: 8
driver_TPOWERDOWN: 20
driver_TBL: 2
driver_TOFF: 3
driver_HEND: 5
driver_HSTRT: 3
driver_PWM_AUTOGRAD: True
driver_PWM_AUTOSCALE: True
driver_PWM_LIM: 12
driver_PWM_REG: 8
driver_PWM_FREQ: 1
driver_PWM_GRAD: 14
driver_PWM_OFS: 36


[tmc2209 extruder]
# connected to E0 Stepper on S6
uart_pin: PA15
tx_pin: PD3
microsteps: 16
run_current: 0.8
sense_resistor: 0.110
stealthchop_threshold: 0
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

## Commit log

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2020-04-13 Getting ready for beta
    [A-Duet2_Duex5_Mount_Plate_2.stl, A-Fan_Duct.stl, A-Foot_Base_4.stl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]
2020-04-16 Drawers and Build Cost
    [B-Drawer_End_Cap_2-X.stl, B-Drawer_Support-X.stl]
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2020-04-23 Breakaway Anti CrashCarriages
    [A-X_Upper_Carriage_Block_MGN12_2.stl, A-X_Upper_Carriage_Block_MGN15_2.stl, A-Y_Lower_Carriage_Block_MGN12_2.stl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]
2020-07-20 Git the git to latest CroXY design
    [1_preheatABS.g, 2_preheatPC+.g, 3_preheatPETG.g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]
2020-07-20 Plain Z Lifters
    for those afraid of crocodiles
    [A-Maxwell_Vee_Block.stl, A-Z_Lifter_Plain_3.stl, B-BK_Mount_3.stl]
2020-08-20 Aluminum parts as STEPs
    [BF_Mount_3_Alu.stp, BK_Mount_3_Alu.stp, Bed.stp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]
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2020-09-12 Getting ready for V1.1
    [A-AC_Wago.stl, A-Ballscrew_Alignment_Helper_2.stl, A-DC24V_Wago.stl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]
2020-09-12 Rail alignment tool from Xile
    [3060_RailAlignment.STL]
2020-09-12 No Magneham Z lifter option
    [A-AC_Wago.stl, A-DC24V_Wago.stl, A-Duet2_Duex5_Mount_Plate_Waste_o_Plastic_2.stl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]
2020-09-12 STP export. Reorg of directories
    [3060_RailAlignment.STL, A-AC_Wago-L.stl, A-AC_Wago-L.stp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]
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2020-09-17 Updated motor bases to Misumi Shoulder screw
    Motor bases used to use a McMaster part. Misumi MSB5-35 costs a lot less, but has slightly different geometry
    [A-Motor_Base_X_2-T.stl, A-Motor_Base_X_2-T.stp, A-Motor_Base_Y_2-T.stl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]
2020-09-17 forgot to rotate the STLs
    [A-Motor_Base_X_2-T.stl, A-Motor_Base_X_2.stl, A-Motor_Base_Y_2-T.stl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]
2020-09-17 Flip print orientation of BK_Thin
    [B-BK_Mount_Thin_3-B.stp, B-BK_Mount_Thin_3.stl]
2020-09-17 1515 variants of XY blocks - Untested
    [A-X_Carriage_Block_1515_2-B.stp, A-X_Carriage_Block_1515_2.stl, A-X_Carriage_Block_2-B.stp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]
2020-09-17 1515 Tee Nuts for 1515 Cross raill backers
    [B-1515_Tee_Nut_4-X.stp, B-1515_Tee_Nut_4.stl]
2020-09-17 Thicker version - Use if your first layer is 0.2mm not 0.3mm
    [B-1515_Tee_Nut_Thicker_4-X.stp, B-1515_Tee_Nut_Thicker_4.stl]
2020-09-19 Update B-Probe_Dock_Hemera_Front.stl
    Cleanup chamfers
    [B-Probe_Dock_Hemera_Front.stl]
2020-09-24 Blocks that support MGN12 or MGN15.
    What i'm running currently. Moving to the 1515 variant that captures the 1515 extrusion
    [A-X_Carriage_Block_1215_2-B.stp, A-X_Carriage_Block_1215_2.stl, A-Y_Carriage_Block_1215_2-B.stp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]
2020-09-24 Push current version
    XY blocks to change soon
    [A-Fan-Duct-X.stp, A-Hemera Mount_Lower-R.stp, A-Hemera Mount_Lower.stl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]
2020-09-24 Delete A-Motor_Base X_2.stl
    Cleanup
    [A-Motor_Base X_2.stl]
2020-09-24 Print orientation of caps fixed. RRF Config
    [A-X_Carriage_Block_1215_2-B.stp, A-X_Carriage_Block_1215_2.stl, A-Y_Carriage_Block_1215_2-B.stp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]
2020-09-25 Z switch mount print wall fixes.
    [B-Z_Touch_Switch_Mount-F.stp, B-Z_Touch_Switch_Mount.stl]
2020-09-26 Hemera V2 Crux toolhead
    Printing and working.
    [A-Fan-Duct-X.stp, A-Hemera Mount_Lower-R.stp, A-Hemera Mount_Lower.stl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]
2020-09-26 Updated STLs for 1515 captured rail backer by XY cars
    [A-AC_Wago-L.stp, A-AC_Wago.stl, A-DC24V_Wago-L.stp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]
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2020-10-11 Jean Claude Damn Chamfer
    [A-MGN12_15_Alignment-F.stl, A-MGN12_20_Alignment-F.stl, A-MGN12_30_Alignment-F.stl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]
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2020-10-12 FysectS6 + BTT Expander Mount
    [3060_RailAlignment.STL, B-Fysetc_S6_BTT_Mount-F.stp, B-Fysetc_S6_BTT_Mount.stl]
2020-10-12 Pi, Expander, S6 Mounts separate.
    [B-BTT_EXP_MOT_Mount-F.stp, B-BTT_EXP_MOT_Mount.stl, B-Fysetc_S6_BTT_Mount.stl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]
2020-10-13 electronics mount higher and less wide. CroXY bed png
    [B-BTT_EXP_MOT_Mount-F.stl, B-BTT_EXP_MOT_Mount-F.stp, B-BTT_EXP_MOT_Mount.stl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]
2020-10-13 Integrated Z motor mount
    [B-BK_Mount_Thin_Motor_3-F.stp, B-BK_Mount_Thin_Motor_3-T.stp, B-BK_Mount_With_Motor_3-F.stp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]
2020-10-13 slightly more space between motor and bk10
    [B-BK_Mount_With_Motor_3-T.stp, B-BK_Mount_With_Motor_3.stl]
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2020-10-15 32mm rail spacing, cross extrusions captured by shoulder screws, alt z motor mount, electronic bracket updates
    32mm rail spacing, cross extrusions captured by shoulder screws, alt z motor mount, electronic bracket updates
    [A-AC_Wago-L.stp, A-AC_Wago.stl, A-Ballscrew_Alignment_Helper_2.stl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]
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2020-10-16 make belt slots a little taller so 12mm belts fit. Bracket tweaks
    [A-X_Carriage_Block_1215_2-B.stp, A-X_Carriage_Block_1215_2.stl, A-X_Carriage_MGN12_1515_2-B.stp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]
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2020-10-21 Filament Guide (prevents overrides), endstop block fixes
    [A-Croc_Filament_Guide_2-X.stp, A-Croc_Filament_Guide_2.stl, A-Y_Endstop_Block_Y_Max_MGN12_2.stl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]
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2020-11-03 Cleaned up XY blocks and better endstop wire routing
    [A-Maxwell_Vee_Block_3.stl, A-Maxwell_Vee_Constrained.stl, A-Motor_Base_X_2.stl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]
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2020-11-05 QOL ease of installation improvements. new heatsert in fixed belt
    [A-X_Carriage_MGN12_1515_2.stl, A-Y_Carriage_MGN12_1515_2.stl, B-XY_Carriage_Cap_MGN12_1515_4.stl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]
2020-11-05 recess heatsert so m3x20 works for both 12mm and 9mm belts
    [A-X_Carriage_MGN12_1515_2-B.stl, A-Y_Carriage_MGN12_1515_2-F.stl, B-XY_Carriage_Cap_MGN12_1515_4-F.stl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]
2020-11-08 Stepper Jack for Z steppers to prevent slight deflection under load
    [B-Stepper_Jack_3-F.stp]
2020-11-08 Stepper Jack for under Z motors to prevent deflection
    [B-Stepper_Jack_3.stl]
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2020-11-15 fixes for inadvertant checkins.
    [A-CroXY_Switch_Arrow_2.stl, A-Fan-Duct-X.stp, A-Foot_Base_4-F.stp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]
2020-11-15 Fix Rotations
    [A-X_Carriage_MGN12_1515_2.stl, A-Y_Carriage_MGN12_1515_2-F.stp, A-Y_Carriage_MGN12_1515_2.stl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]
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2020-12-19 Blower mount brackets for cooling SKR/S6 with 5015 fan
    [B-S6_Blower_Mount-F.stp, B-S6_Blower_Mount.stl, B-SKR_Blower_Mount-F.stp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]
2020-12-19 Support both Heatserts and Self Tapping into plastic.
    [B-S6_Blower_Mount-F.stp, B-S6_Blower_Mount.stl, B-SKR_Blower_Mount-F.stp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]
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2021-01-05 Alignment helpers stiffer
    [A-MGN12_15_Alignment-F.stl, A-MGN12_15_Alignment-F.stp, A-MGN12_20_Alignment-F.stl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]
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2021-02-07 Mirror Version of Sailfin and some minor tweaks
    [Front-R.stp, Front.stl, Front_Mirror-R.stp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]
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2021-02-11 Sailfin and fix bug in endstops
    [A-Sailfin_Toolhead_7525_Ducts-X.stp, A-Sailfin_Toolhead_7525_Ducts.stl, A-Sailfin_Toolhead_Body.stl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]
2021-02-11 sailfin stp and fix bad rotations
    [B-Endstop_Block_A_2-B.stl, B-Endstop_Block_A_2.stl, B-Endstop_Block_B_2-B.stl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]
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2021-02-17 microxy Z fixes
    [A-Left_Bed_Mount-T.stl, A-Left_Bed_Mount-T.stp, A-Left_Bed_Mount.stl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]
2021-02-17 Delete B-No_BK10_Ball_Screw_Spacer_3.stl
    no longer needed
    [B-No_BK10_Ball_Screw_Spacer_3.stl]
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2021-03-17 Minor Sailfin Interference, microxy stuffs
    [A-Front_Bed_Mount_180-B.stp, A-Front_Bed_Mount_180.stl, A-Left_Bed_Mount-T.stp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]
2021-03-22 Sailfin rear screw no longer protrudes
    [Front-R.stp, Front.stl, Front_Mirror-R.stp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]
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2022-02-05 13 and 19mm CF spring support. Stepper drill guide
    [A-Stepper_M4_Drill_Tap_Jig.stl, A-Z_13mmSpring_Bearing_Spacer_6.stl, A-Z_13mmSpring_Body_3.stl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]
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2022-02-07 Redo the fzcked toolhead ducts and such. move euclid probe so doesn't get picked up accidentally when homing
    [A-Foot_Base_4.stl, A-Foot_Top_4.stl, A-Handle_Croxy.stl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]
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2022-02-14 Z Refinements. Maybe even mirrored stuff properly exported.
    [A-AC_Wago.stl, A-DC24V_Wago.stl, A-Foot_Base_4.stl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]
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2022-03-08 fix naming of motor plates
    [A-X_Motor_2.stl, A-Y_Motor_2.stl, X_Motor_2.stl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]
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2022-03-08 Missing Cforce Spring Spacers.
    [B-13mm_CForce_Spring_Inner_Spacer_6.stl, B-13mm_CForce_Spring_Outer_Spacer_12.stl, B-19mm_CForce_Spring_Inner_Spacer_6.stl]
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2022-03-14 cad. has some minor errors
2022-03-14 drawer bottom fix
    [A-Handle_Croxy.stl, B-Drawer_Corner_Front_Left.stl, B-Drawer_Corner_Front_Right.stl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]
2022-03-18 led slot covers and more magnet clearance
    [A-Maxwell_500x125_Magnets_3.stl, A-Slot_Covers_LED_Scale_Appropriately.stl, A-Slot_Covers_Scale_Appropriately.stl]
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2022-03-19 new XY cars, use posidrive on endstop covers
    [A-X_Front_2020.stl, A-X_Front_20mm_CF.stl, A-X_Front_CF20.stl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]
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2022-03-31 fix the derpy missing hole in CF spring
    [A-Maxwell_500x125_Magnets_3.stl, A-Upper_Idler_Spacer_9.stl, A-Z_Belt_Red_Base_3.stl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]
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2022-04-17 fix derp drill guides
    [B-Bed_Drill_Guide_LFront.stl, B-Bed_Drill_Guide_Left.stl, B-Bed_Drill_Guide_RFront.stl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]
2022-04-20 XY Strengthening screw comes from below now. (else would require 29mm len screw)
    [A-X_Front_2020.stl, A-X_Front_20mm_CF.stl, A-X_Rear_2020.stl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]
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2022-05-16 CF Tube Fixes
    [A-X_Front_20mm_CF.stl, A-X_Front_25mm_CF.stl, A-Y_Left_20mm_CF.stl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]
2022-05-16 Belt clearance for all
    [A-X_Front_20mm_CF.stl, A-Y_Left_2020.stl, A-Y_Right_2020.stl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]
2022-05-19 toolhead fixes for AJ
    [A-Duct.stl, A-Top.stl, B-Back_Plate.stl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]
2022-05-23 mast fixes
    [A-Top.stl, B-Back_Plate.stl, B-Mast.stl]
2022-05-23 mast fix
    [A-Duct-T.stl, A-Top-X.stl, B-Back_Plate-B.stl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]
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
